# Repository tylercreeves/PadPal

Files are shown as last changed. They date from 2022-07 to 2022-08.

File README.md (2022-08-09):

# PadPal

> Author: Tyler Reeves, AKA T-Rex ([@tylercreeves](https://github.com/tylercreeves))

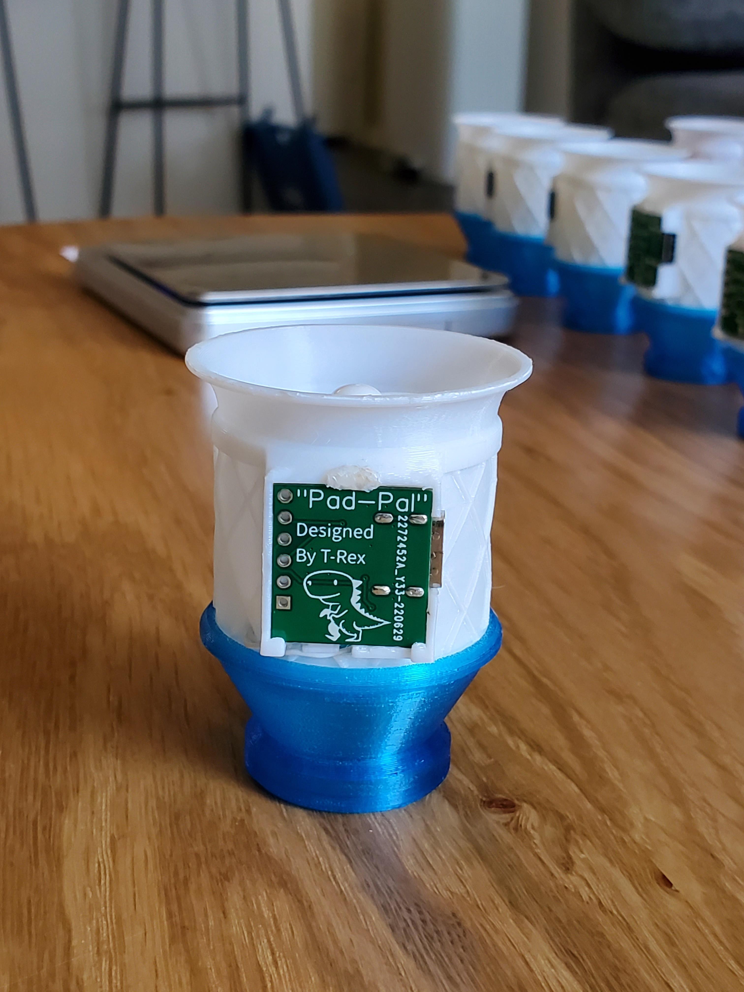
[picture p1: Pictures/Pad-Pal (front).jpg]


**An untralight electric sleeping pad inflator solution**

The PadPal is a bare bones, simple electric sleeping pad inflation device. The goal of this project is to make a sleeping pad inflator that us UL folks would not shun away in flavor of sore jaw muscles, empty lungs, and light heads.

Below is a breakdown of the project as well as how you can make your own. 

If making your own seems like a hassel, you can also purchase them from me for $44.00 shipped to the lower 48 states (contact me for shipping rates elsewhere) by reaching out to me via reddit u/tylercreeves

## Design

The PadPal is designed to leverage consumer grade 3D printing technology and consumer accessible PCB manufactures like JLCPCB. It is composed of 5 parts.

>**Part:** 3D printed fan duct housing

**Qty:** 1

>**Part:** 3D printed sleeping pad valve adapter

**Qty:** 1

>**Part:** 6x15mm coreless DC motor with .8mm shaft and micro JST connector

**Qty:** 1

>**Part:** 31mm 4 blade propeller with .8mm press fit shaft hole.

**Qty:** 1

>**Part:** PadPal V3 PCB with SMD

**Qty:** 1

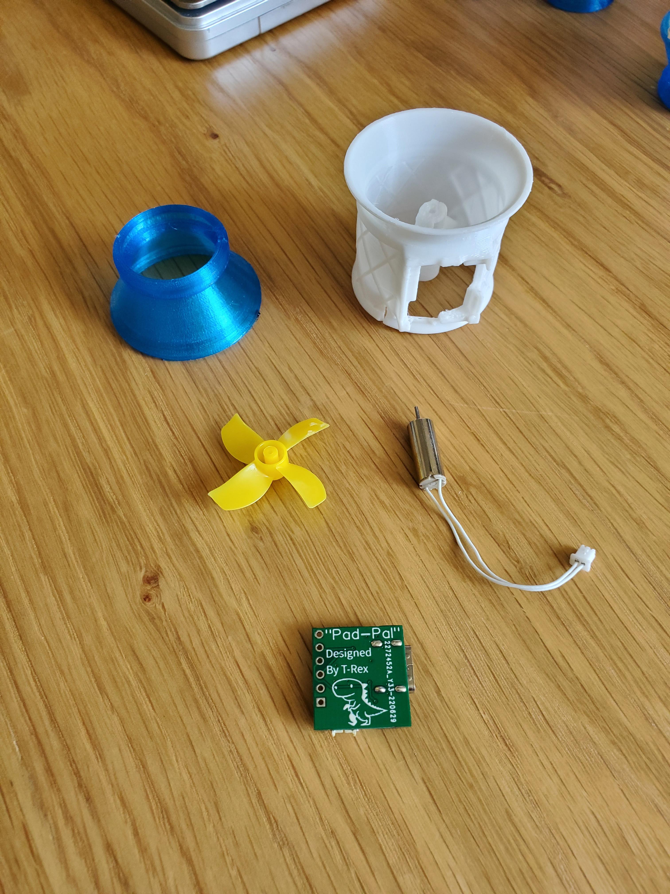
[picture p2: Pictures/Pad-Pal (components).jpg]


## 3D Printed Hardware

There are 2 user printed parts that compose the PadPals general body. Bellow are printing suggestions for each part.

>**Part:** PadPal_Duct_V3

**Material:** Polycarbonate

**Settings:** Use custom support structures to support the motor housing, bridges for the PCB housing, and chamerfered bridges from motor housing to inner fan duct. Here is a picture of the areas I added custom support enforcers. A brim may help prevent the Polycarbonate from warping.

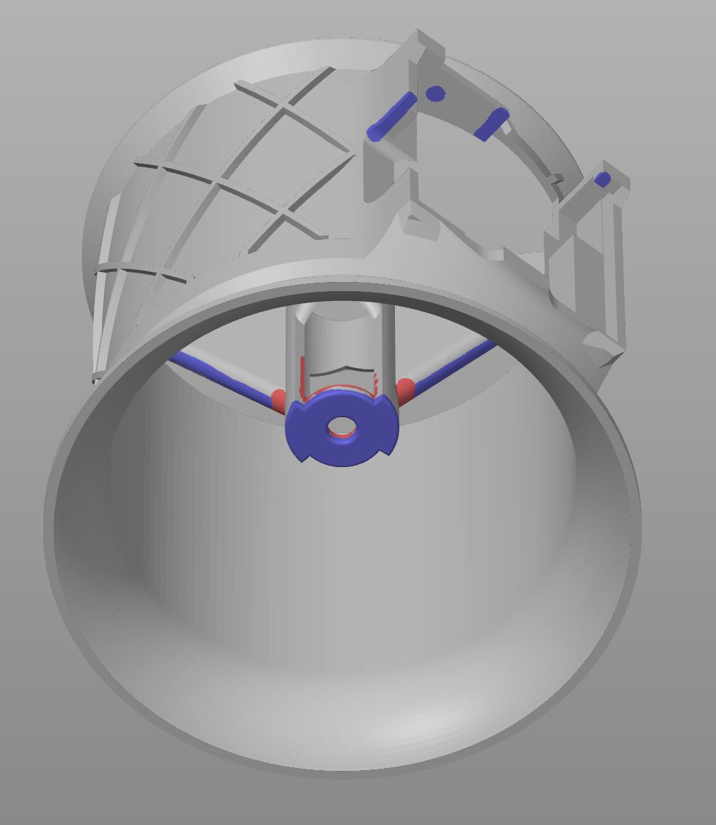
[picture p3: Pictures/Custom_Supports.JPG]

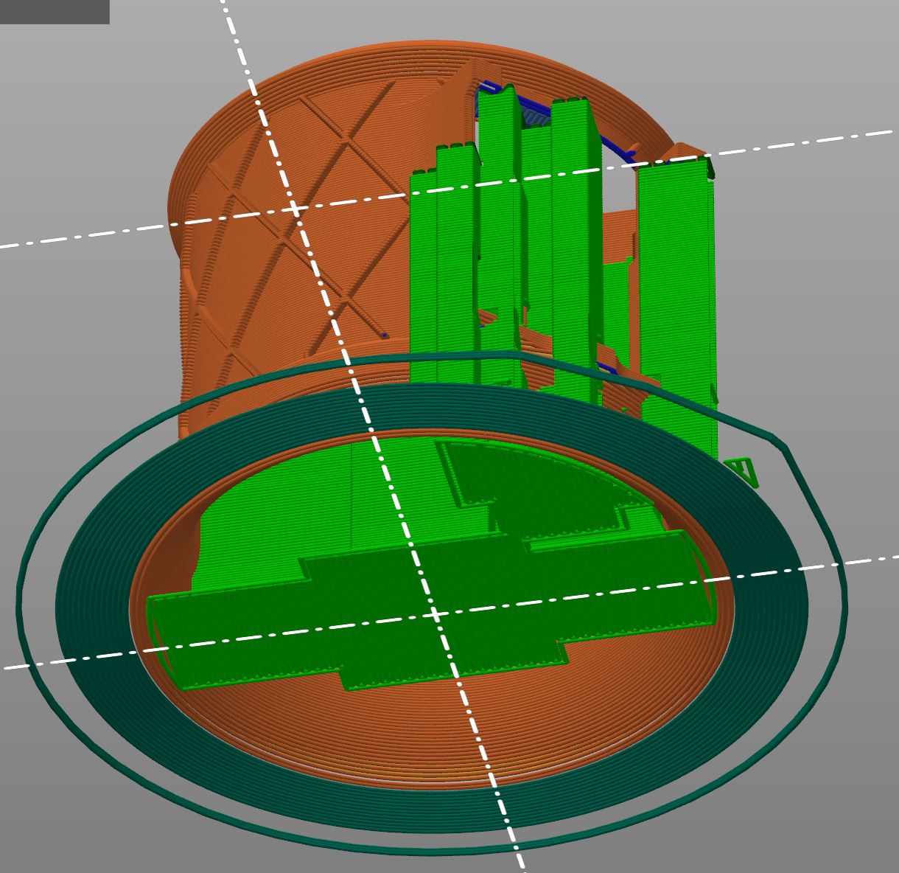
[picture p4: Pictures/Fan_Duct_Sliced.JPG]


>**Part:** PadPal_ThermarestWingLock_V3

**Material:** TPU

**Settings:** print with skinny end facing up, add a 2mm brim, no supports

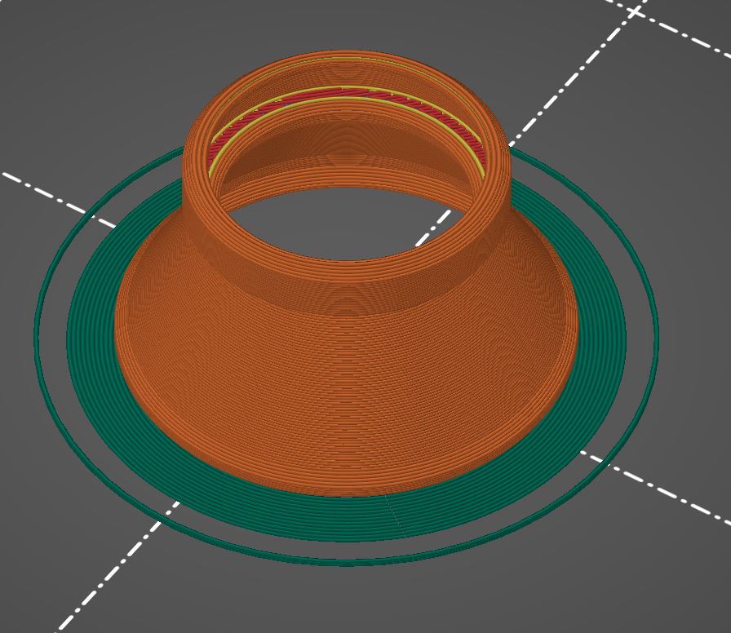
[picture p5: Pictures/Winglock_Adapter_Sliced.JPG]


## Code (Finite State Machine)

The PadPal utalizes an Attiny13ASU microcontroller that can be programmed to controlle the DC motor. I have programmed the MC with a finite state machine that works as follows. When you plug in the device, it waits 2 seconds before starting. After 2 seconds pass, it ramps up the fan to a specified speed. Once at specified speed it maintains that speed for a specified time. Once the specified time has ellapse, it will turn off the fan and enter sleep mode to avoid accidentally draining a forgetful hikers bacttery bank. To restart the PadPal, the user must unplug it and plug it in again.

## Making/Buying the Custom PCB

To get a custom motor controller PCB for this project, you have two options. One is to download the EDA GERBER files, BOM file, and source a manufactureur for the PCB as well as all the components. This board used SMD components and requires some decent skills in SMD soldering to pull off. It you go this route, there usually are minimum order quantities required for the PCB and components, so you may end up with a few extra boards.

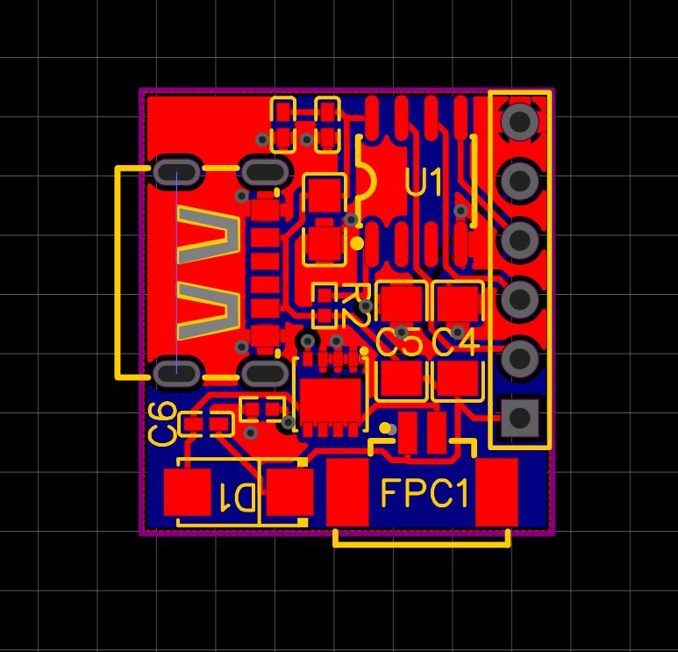
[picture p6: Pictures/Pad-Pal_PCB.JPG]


To save some of you the time and complexity of making and programming the boards yourself, you can contact me via reddit at u/tylercreeves where I sell the assembled and programmed boards for $12.18 shipped to the lower 48 states (contact me for special shipping rates elsewhere).

## Programming the PCB

Assuming you have gone the route of making your own boards, here is how to program the PadPal PCB. You will need to make an "Arduino as ISP". For this I used an Arduino Uno board and purchased a perferate "hat" board to solder up programmer with pogopins. Here are picture of the Arduino uno, custom "hat", and the two together.

 


First you will need to download the Arduino IDE if you havent done so. Next you need to flash the "Arduino as ISP" example sketch into the Arduino You will use to program your PadPal. Now you need to download the MicroCore liberary into your Arduino IDE so you can program the PadPal. Please watch [this video](https://www.youtube.com/watch?v=G2nVVtmKgWI&list=LL&index=113) of an unrelated project on how to do so by Electronics BD.

## Arduino as ISP Programmer Pin-Out

Here is a picture of my setup and Pin-Out of the headers on my custom motor control boards. You might have to do some clever mix and matching between my picture and the linked video untill I put up a complete pin-out for the arduino-ISP programmer I made.

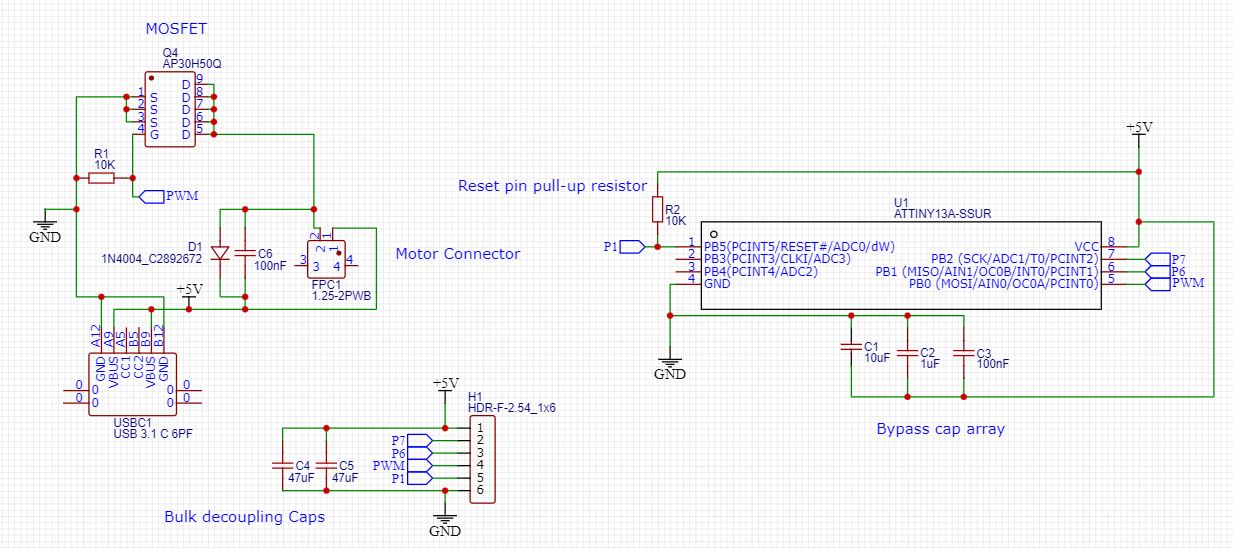
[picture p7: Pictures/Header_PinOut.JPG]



**Bellow is an FSM Diagram to assist in understanding the code so one can modify it.**

Review the FSM diagram along side the included code to get a sense of what is going on in the code. 

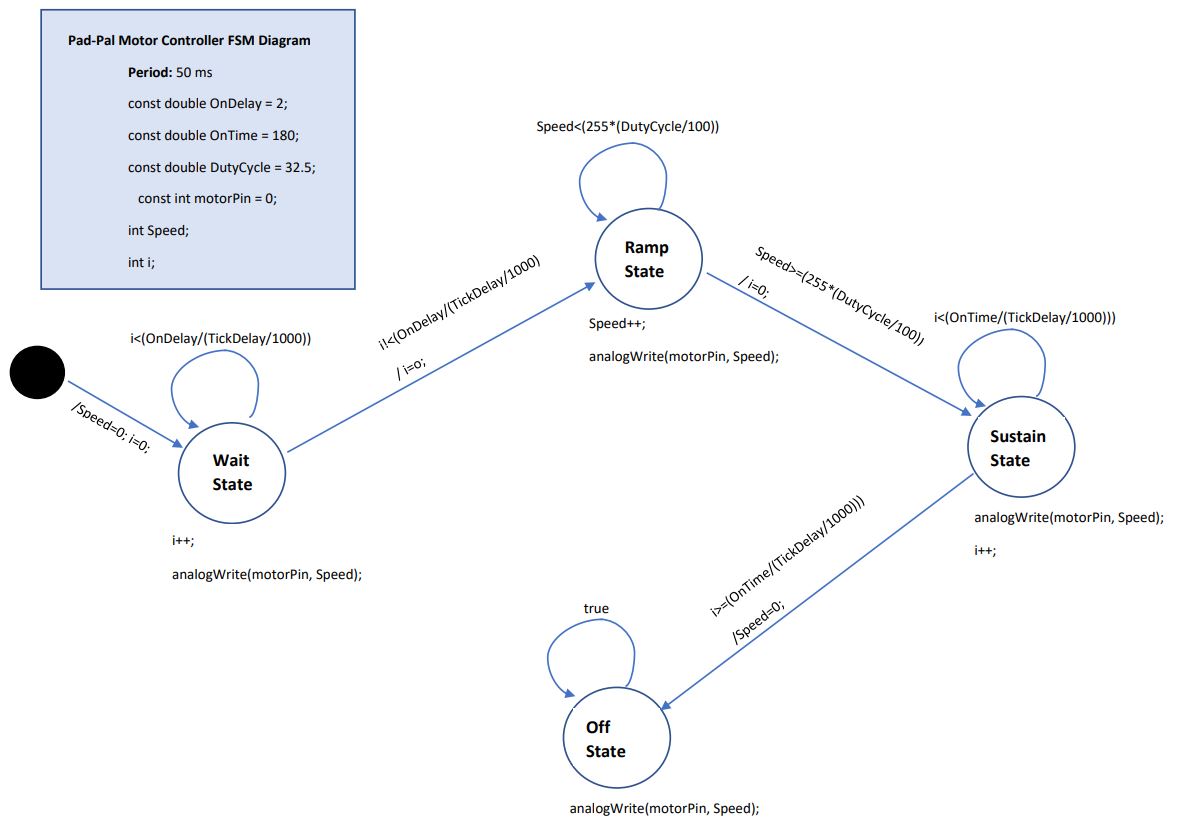
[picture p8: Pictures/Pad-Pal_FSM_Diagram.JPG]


## Assembly/Finishing

After you purchase a board, or finish making, soldering, and programming your own, you are ready for assembly! I'm not even going to tell you how, its pretty simple once all the parts are infront of you your ready. I'd suggest do the motor first, followed by the fan blade, then plugin the motor to the PCB and insert the PCB to its housing. Its a tight fit so you may need to get glever with some soft contact tools to push it in all the way.

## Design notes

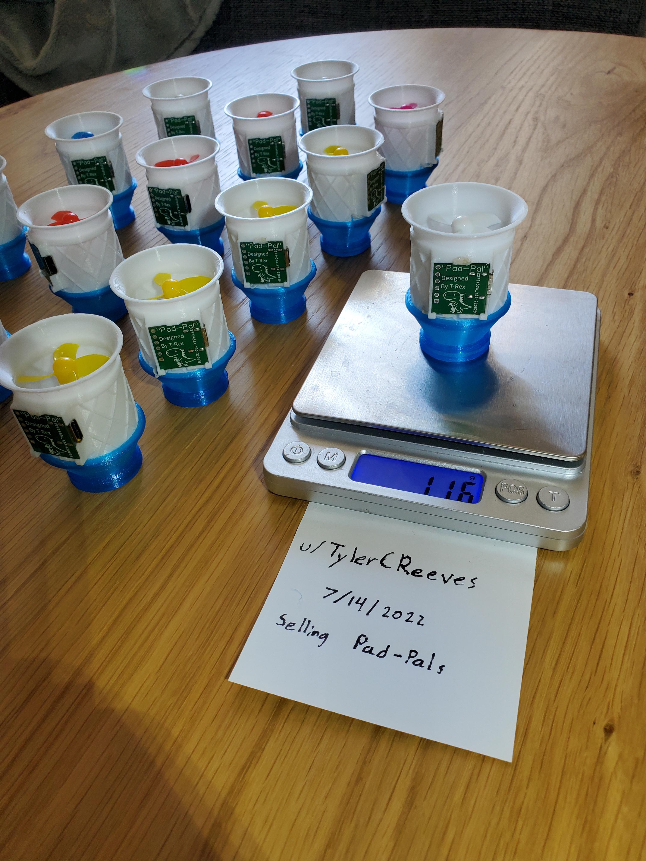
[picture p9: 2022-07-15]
Pictures/Pad-Pals (on scale).jpg

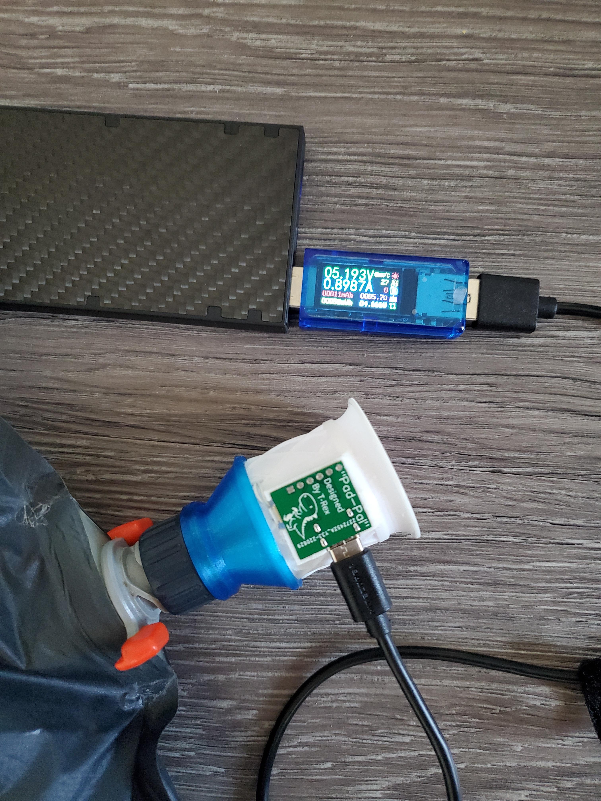
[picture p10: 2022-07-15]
Pictures/Pad-Pals (working).jpg

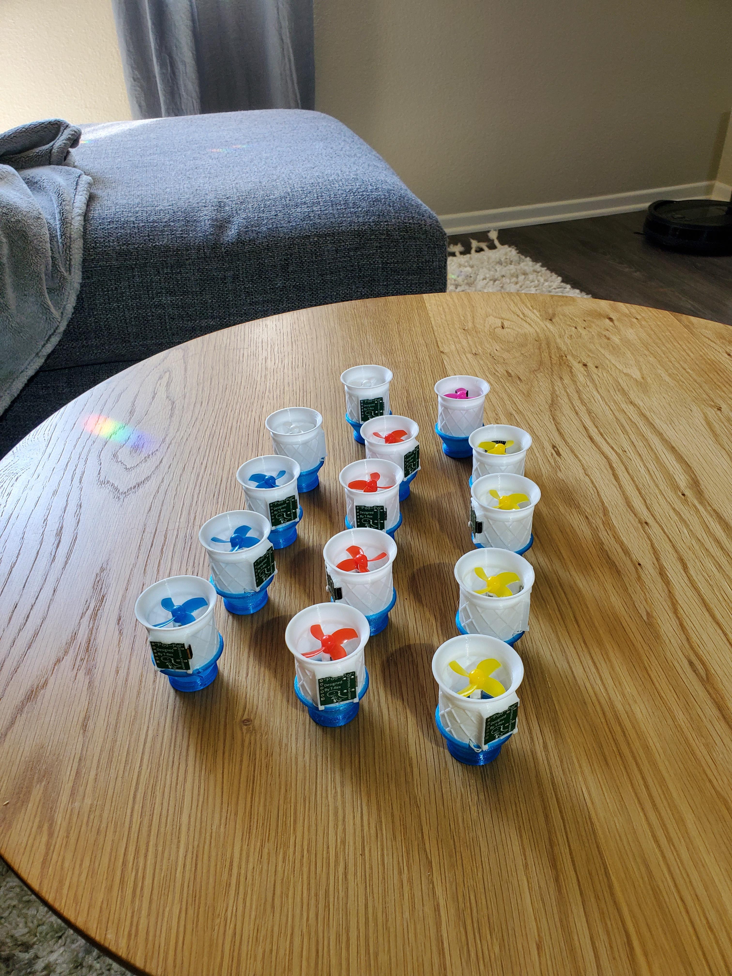
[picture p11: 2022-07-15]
Pictures/All the Pals.jpg

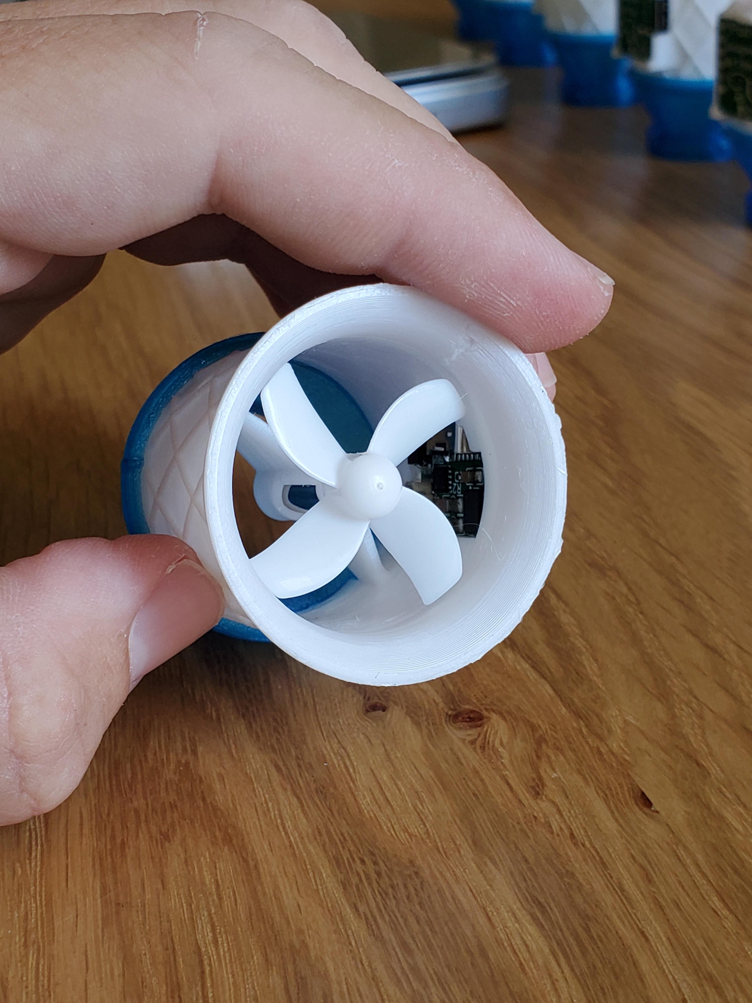
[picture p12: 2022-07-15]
Pictures/Pad-Pals (top).jpg

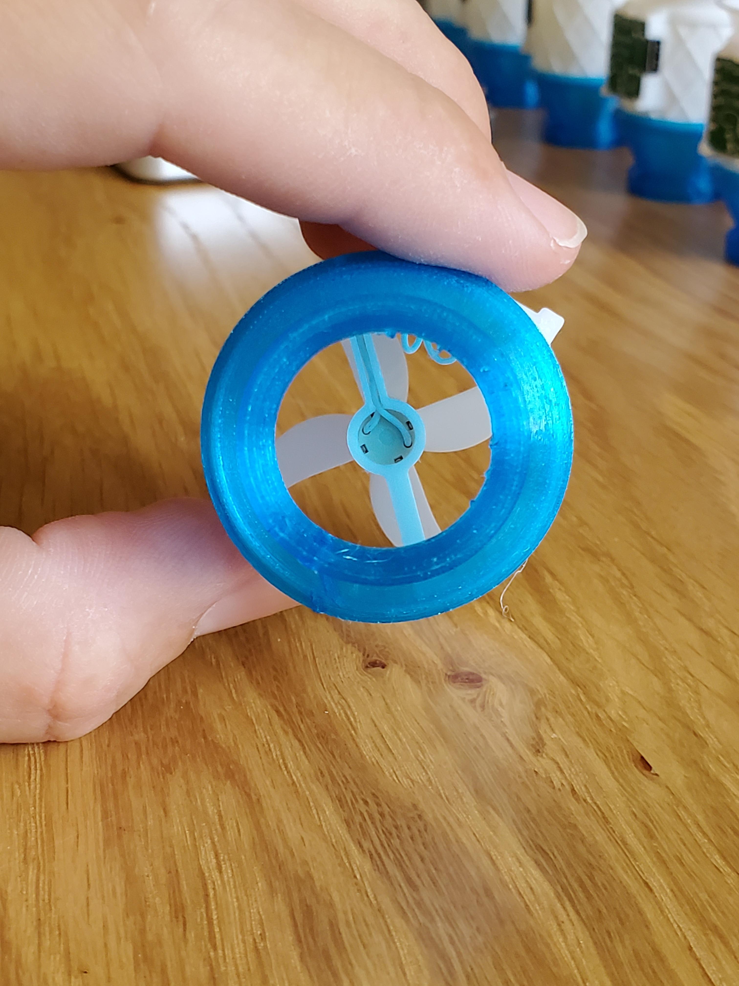
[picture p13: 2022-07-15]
Pictures/Pad-Pal (bottom).jpg

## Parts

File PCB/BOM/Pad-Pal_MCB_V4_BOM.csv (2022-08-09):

ID | Name | Designator | Footprint | Quantity | Manufacturer Part | Manufacturer | Supplier | Supplier Part
1 | 10uF | C1 | C0805 | 1 | GCM21BR71A106KE22L | MuRata | LCSC | C126586
2 | 1uF | C2 | C0402 | 1 | GCM155C71A105KE38D | Murata Electronics | LCSC | C126521
3 | 100nF | C3,C6 | C0402 | 2 | CC0402JRX7R8BB104 | YAGEO | LCSC | C541465
4 | 47uF | C4,C5 | C1206 | 2 | CL31A476MPHNNNE | SAMSUNG | LCSC | C96123
5 | 1N4004_C2892672 | D1 | SMA_L4.3-W2.6-LS5.1-RD | 1 | 1N4004 | YONGYUTAI(永裕泰) | LCSC | C2892672
6 | 1.25-2PWB | FPC1 | CONN-SMD_2P-P1.25_DEALON_1.25-2PWB | 1 | 1.25-2PWB | DEALON(德艺隆) | LCSC | C2905009
7 | HDR-F-2.54_1x6 | H1 | HDR-F-2.54_1X6 | 1 |  |  | LCSC | C40877
8 | AP30H50Q | Q4 | DFN-8_L3.2-W3.1-P0.65-LS3.4-BL | 1 | AP30H50Q | ALLPOWER(铨力) | LCSC | C2849568
9 | 10K | R1,R2 | R0402 | 2 | RT0402BRD0710KL | YAGEO | LCSC | C190095
10 | ATTINY13A-SSUR | U1 | SOIC-8_L5.0-W4.0-P1.27-LS6.0-BL | 1 | ATTINY13A-SSUR | MICROCHIP | LCSC | C40382
11 | 5.1kΩ | U2,U3 | R0402 | 2 | HPCR0402F5K10K9 | ResistorToday | LCSC | C365032
12 | USB 3.1 C 6PF | USBC1 | USB-C-SMD_TYPE-C-USB-13 | 1 | - | LCSC | LCSC | C168701

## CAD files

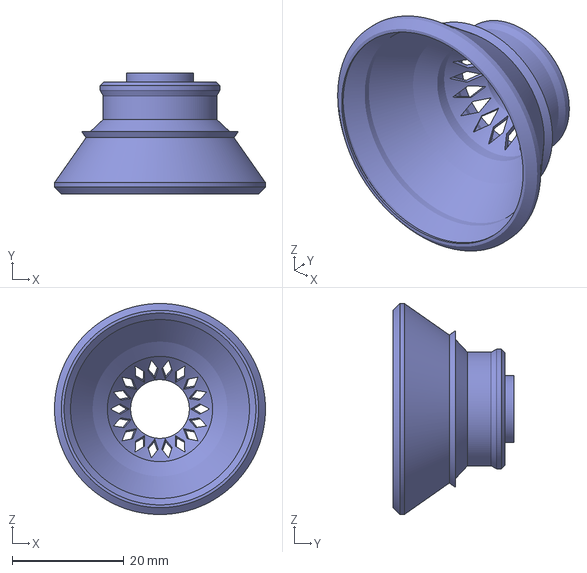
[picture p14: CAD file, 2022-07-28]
Hardware_Files/Mesh_Files(for pirnitng)/Exped Sinmat Addapter/PapPal_ExpedSinmat_1.2.3mf
37.8 x 21.6 x 37.8 mm

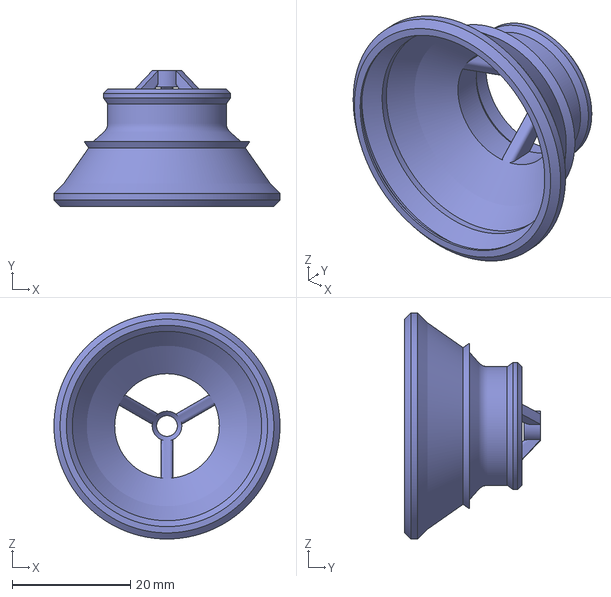
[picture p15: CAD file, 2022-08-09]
Hardware_Files/Mesh_Files(for pirnitng)/Sea to Summit Addapters/Seas2Summit_V1.3.3mf
38.2 x 22.9 x 38.2 mm

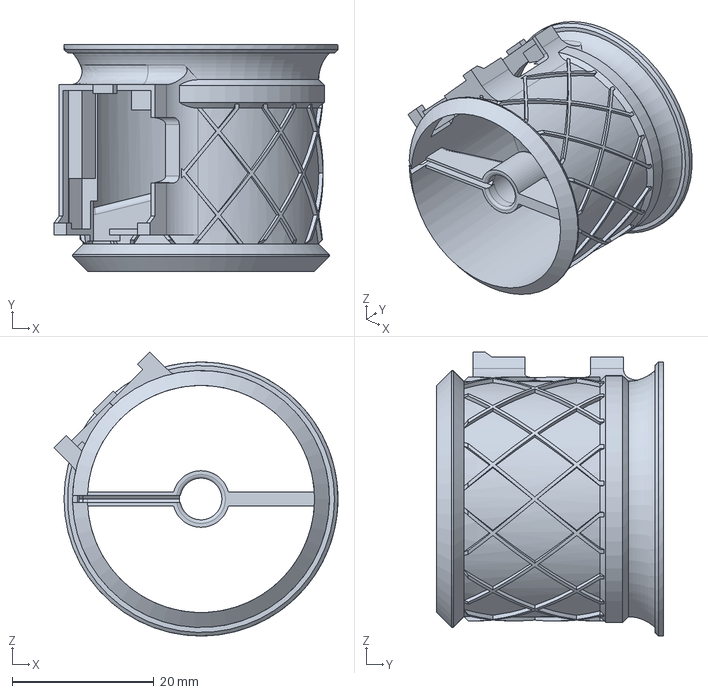
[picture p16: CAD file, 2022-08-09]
Hardware_Files/CAD_Files/Fan Duct/Duct Housing_V3.2.step
40.0 x 31.9 x 40.0 mm

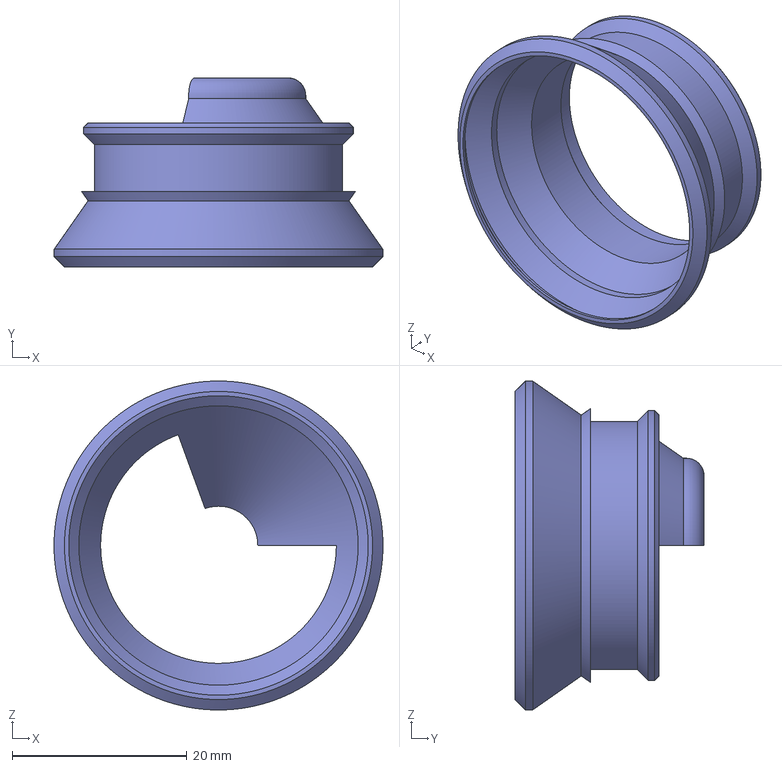
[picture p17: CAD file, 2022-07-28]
Hardware_Files/Mesh_Files(for pirnitng)/Big Agnes Pad Addapters/Big Agnes Valve Adapter 1.1.3mf
37.7 x 21.7 x 37.7 mm

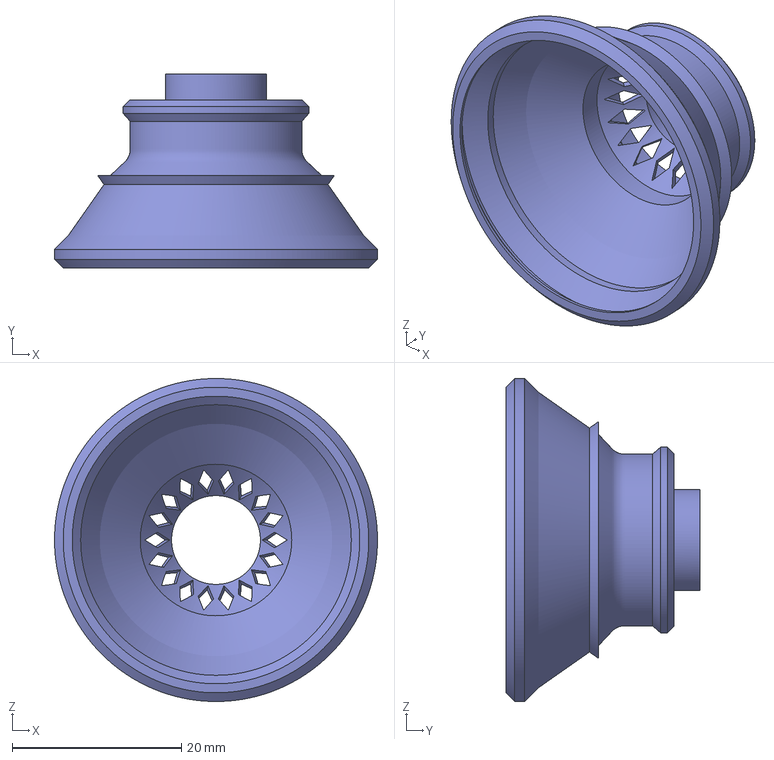
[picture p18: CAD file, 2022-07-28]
Hardware_Files/Mesh_Files(for pirnitng)/Exped Sinmat Addapter/PapPal_ExpedSinmat_V2.3mf
38.2 x 22.9 x 38.2 mm

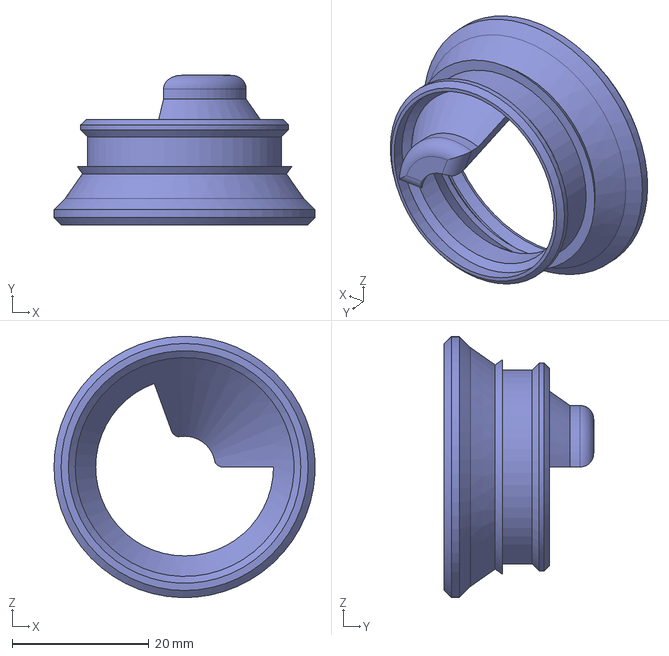
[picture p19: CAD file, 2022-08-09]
Hardware_Files/CAD_Files/Valve Adapters/Big Agnes Valve Addapter.step
38.2 x 21.9 x 38.2 mm

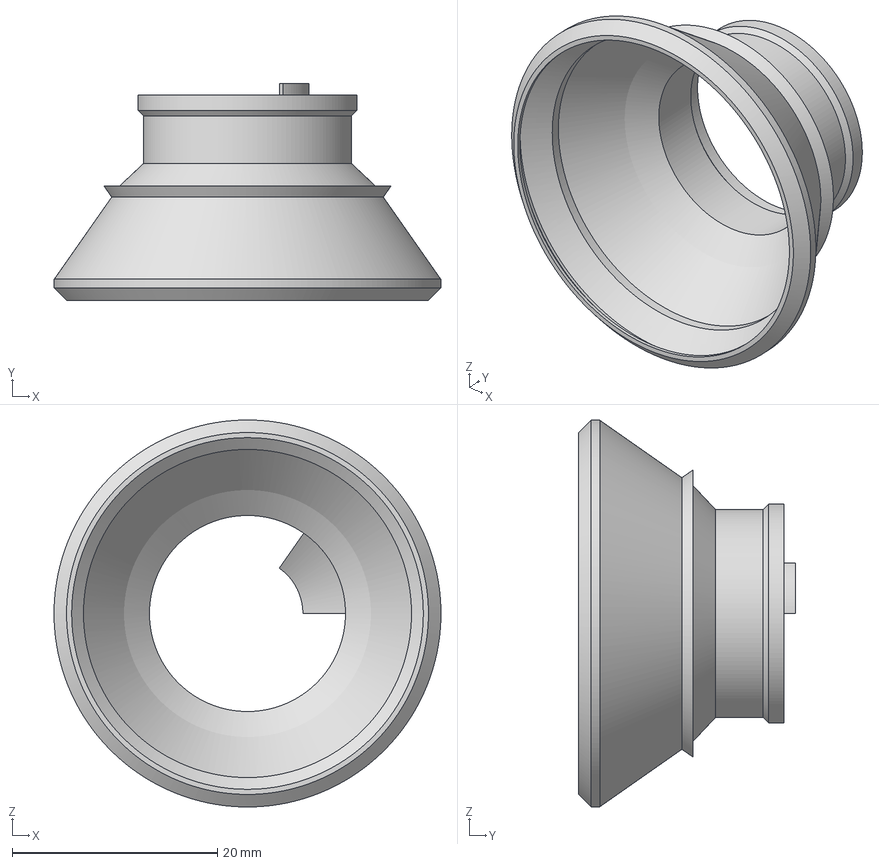
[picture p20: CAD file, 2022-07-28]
Hardware_Files/Mesh_Files(for pirnitng)/Exped Sinmat Addapter/PapPal_ExpedSinmat_1.1.3mf
37.8 x 21.1 x 37.8 mm

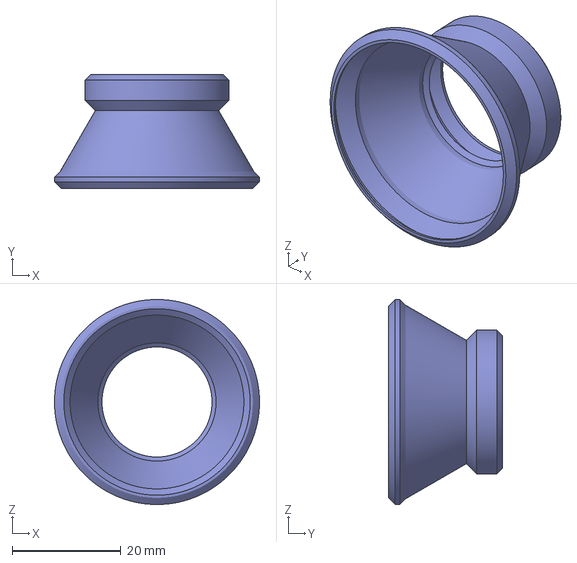
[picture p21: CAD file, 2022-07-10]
Hardware_Files/Mesh_Files(for pirnitng)/Thermarest Adapters/PadPal_ThermarestWingLock_1.3.3mf
37.7 x 21.0 x 37.7 mm

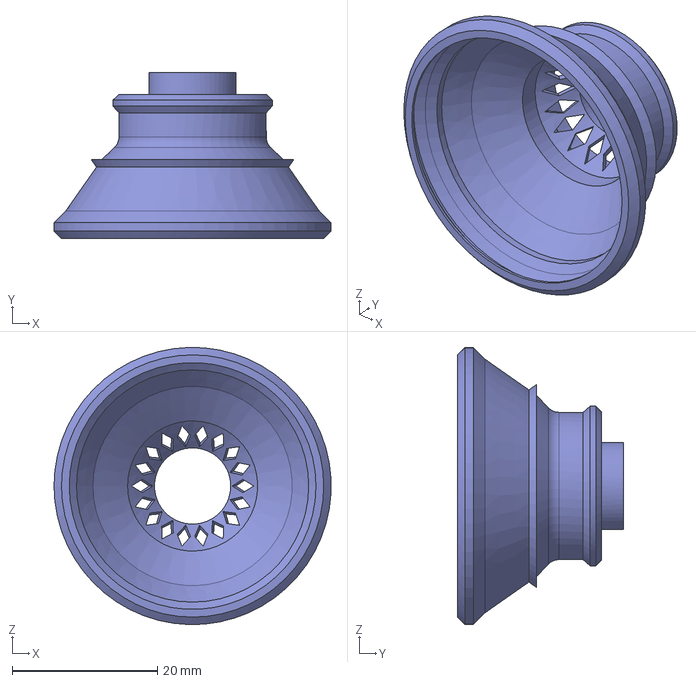
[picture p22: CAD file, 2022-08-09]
Hardware_Files/CAD_Files/Valve Adapters/Exped Sinmat UL Valve Adapter.step
38.2 x 22.9 x 38.2 mm

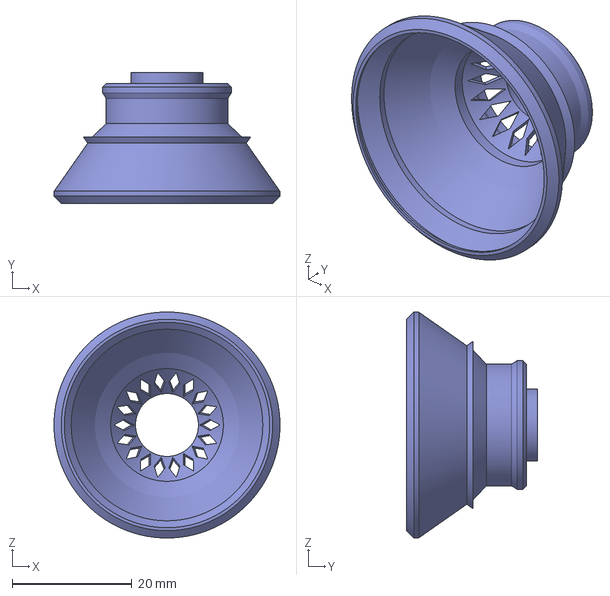
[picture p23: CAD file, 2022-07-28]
Hardware_Files/Mesh_Files(for pirnitng)/Exped Sinmat Addapter/PapPal_ExpedSinmat_1.3.3mf
37.8 x 21.9 x 37.8 mm

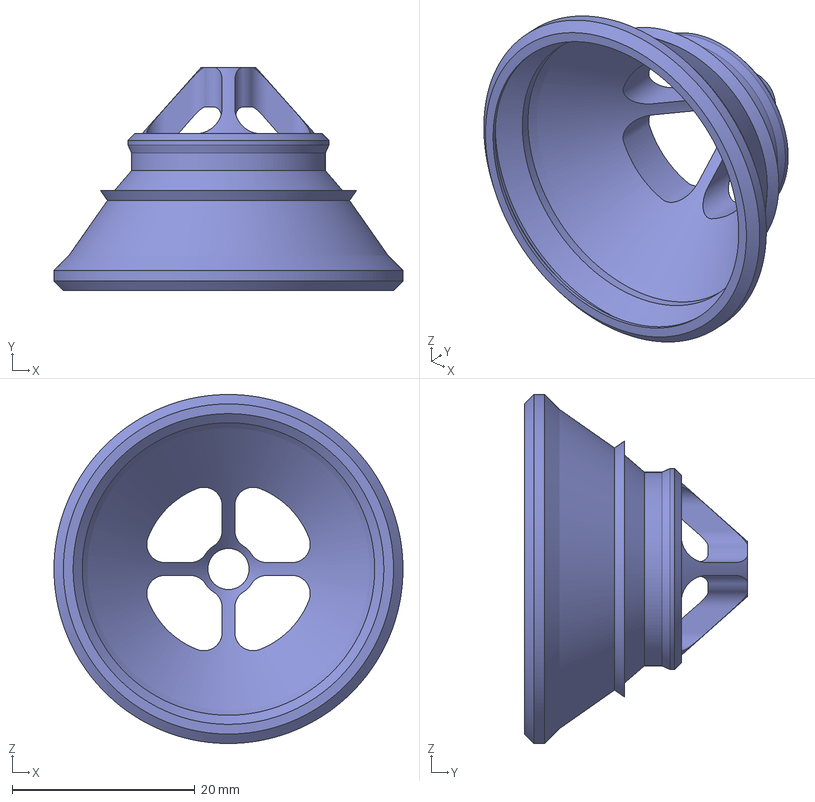
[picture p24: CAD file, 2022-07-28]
Hardware_Files/Mesh_Files(for pirnitng)/Nemo Pad Coupler/Nemo_CoupLer_V1.3.3mf
38.2 x 24.4 x 38.2 mm

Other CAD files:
Hardware_Files/CAD_Files/Valve Adapters/Sea to Summit Valve Addapter.step
Hardware_Files/Mesh_Files(for pirnitng)/Fan_Duct/PadPal_Duct_V3.3.3mf
Hardware_Files/CAD_Files/Valve Adapters/Nemo Tensor Insulated Valve Addapter.step
Hardware_Files/Mesh_Files(for pirnitng)/Exped Sinmat Addapter/PapPal_ExpedSinmat_1.9.3mf
Hardware_Files/Mesh_Files(for pirnitng)/Big Agnes Pad Addapters/Big_Agnes_Valve_Adapter_V1.5.3mf
Hardware_Files/Mesh_Files(for pirnitng)/Exped Sinmat Addapter/PapPal_ExpedSinmat_1.6.3mf
Hardware_Files/CAD_Files/Valve Adapters/PadPal_ThermarestWindLockValve_V3.step
Hardware_Files/CAD_Files/Fan Duct/Duct Housing_V3.1.step
Hardware_Files/CAD_Files/Valve Adapters/Old Nemo Twist Valve Addapter.step
Hardware_Files/CAD_Files/Valve Adapters/Old Thermarest Twist Valve Adapter.step
Hardware_Files/Mesh_Files(for pirnitng)/Big Agnes Pad Addapters/Big_Agnes_Valve_Adapter_V1.2.3mf
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

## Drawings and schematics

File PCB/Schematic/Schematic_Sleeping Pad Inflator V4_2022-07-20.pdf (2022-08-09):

## MOSFET

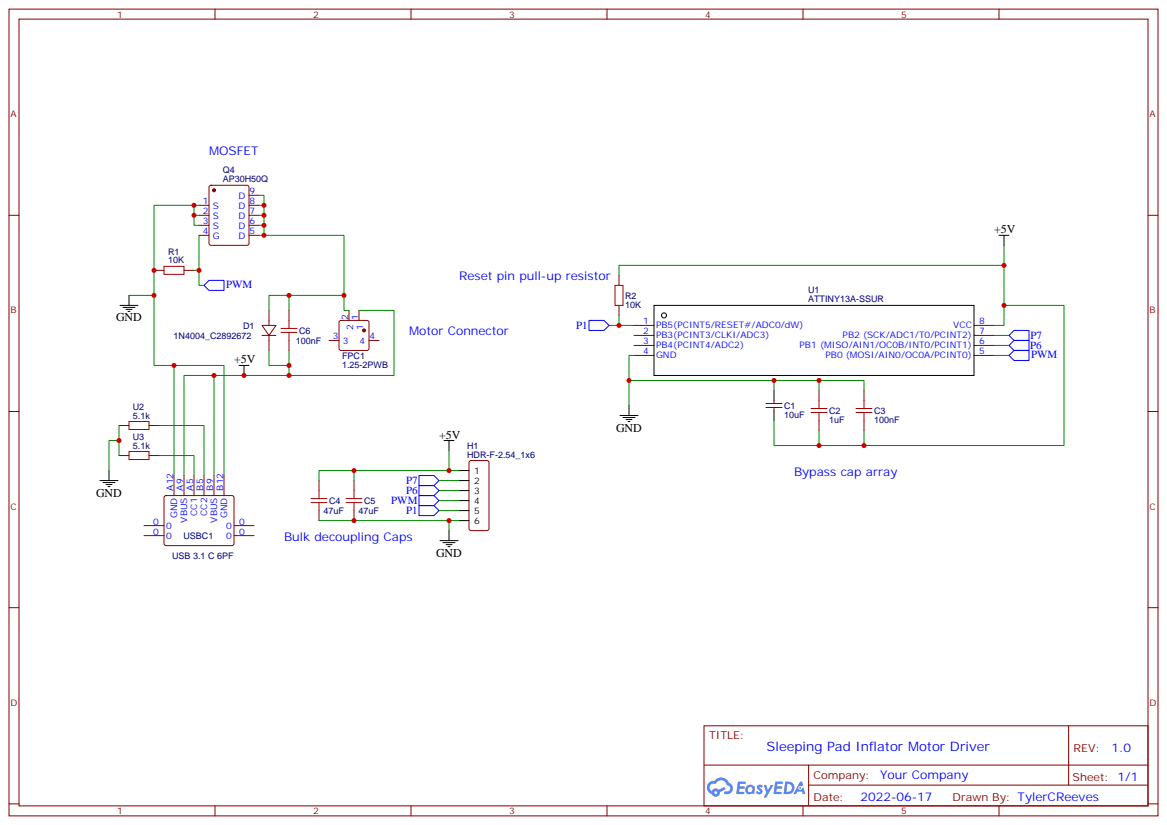
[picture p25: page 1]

Reset pin pull-up resistor

GND B12 VBUS B9 CC2 B5 CC1 A5 VBUS A9 GND A12

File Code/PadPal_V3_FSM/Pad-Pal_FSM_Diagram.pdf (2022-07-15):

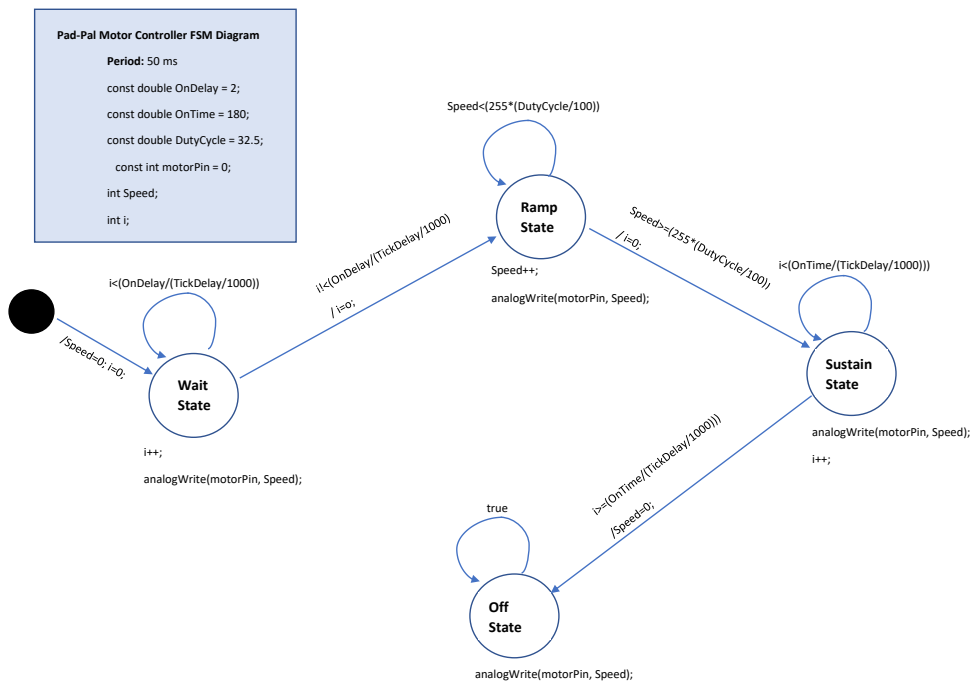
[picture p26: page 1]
i<(OnDelay/(TickDelay/1000)); Speed<(255*(DutyCycle/100)); Speed++;; i<(OnTime/(TickDelay/1000))); true; Period: 50 ms; int Speed;; int i;; Wait State; Ramp State; Sustain State; Off State

Pad-Pal Motor Controller FSM Diagram

const double OnDelay = 2;

const double OnTime = 180;

const double DutyCycle = 32.5;

const int motorPin = 0;

analogWrite(motorPin, Speed);

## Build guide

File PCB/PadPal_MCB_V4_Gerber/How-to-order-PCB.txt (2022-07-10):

How to Order PCB

Please refer to:
https://docs.easyeda.com/en/PCB/Order-PCB

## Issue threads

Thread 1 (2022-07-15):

USBC PD issue

qxtman, 2022-07-15:
Hey, I don't have mine in hand yet, but going off of Schematic V3,
At present, you do not have any resistors on the CC1 or CC2 lanes of the USB C connector.
I believe that those resistors are required when using a propper USB C supply.
Attaching a 5.1k pull down resistor to each pin will (should) re enable USBC to USBC functionality.
I have mine on the way, I will see if I can update my model to prove it out.

There are more details with USB C PD, about forcing lower maximum current, but I do not have enough details on that at present.

tylercreeves, 2022-07-20:
Thanks qxtman!!
Just created a new branch for motor control board V4 where I'm trying to implement the USB-C to USB-C functionality.
I took a V3 board and did a hack job at adding the resistors as described. Interestingly, it worked via USB-C ports on both my power banks, but did not work from a USB-C wall powered power source. IDK whats going on there but it really only has to work with power banks so that left me satisfied enough to implement the changes in a new board.
I'll be uploading the V4 board Gerber files later today, and I should have 20 V4 boards coming in the mail soon (about a week). I'll merge the branch back with main if everything pans out after testing.

tylercreeves, 2022-07-28:
V4 Boards are in and undergoing testing. They appear to work flawlessly : ) I plan to be merging the Motor_Control_Board_V4 branch with main soon.

tylercreeves, 2022-08-10:
I think its solved, V4 board have been working great and snuck them into a few customer Pad-Pals with no issues. I'll be closing this issue for now unless something else pops up.

Closed 2022-08-10.

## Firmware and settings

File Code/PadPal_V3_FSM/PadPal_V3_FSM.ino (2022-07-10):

/*Author: Tyler Reeves
 *Purpose: A finite state machine to control the motor of a sleeping pad inflator.
 *This program works by transitioning between states (each state performs a unique function) based on user selected transition conditions.
 *
*/


//Inflator user paramiters
const double OnDelay = 2;         //OnDelay is the time in seconds the inflator will wait to start the fan after being pluged in
//const double RampDelay = 5;     //time in seconds the fan will ramp up to max speed. Note, not compatible with AttinyA13 MC, uncomment for additional functuionality if you'r using an MC with more flash memmory
const double OnTime = 120;        //OnTime is the time the inflator will stay on in seconds.
const double DutyCycle = 20;      //Max fan speed in terms of percentage. EX: if DutyCycle = 35, then fan will max out at 35% speed. WARNING, depending on motor installed, DutyCycle >= 45 may cause overheating and damage

//peramiters governing finite state machine behavior
const int motorPin = 0;           //Which microcontroller pin sends out the PWM signal?
const double TickDelay = 50;      //Time between state transitions in milliseconds

//Finite State Machine variables
int Speed;                        //Speed is used to ramp up and down fan speed during state ticks. If Speed == 0 no fan, if Speed==255 Max fan.
int i;                            //used to keep track of # of ticks through a given state of the finite state machine

enum States{Wait, Ramp, Sustain, Off} State = Wait; //Declare the states of the finite state machine and set the initial starting state.


void setup()
{
  pinMode (motorPin, OUTPUT);
  Speed=0;
  i=0;
  
}

void Tick(){
  switch(State){ // State transitions
    case Wait:
    if(i<(OnDelay/(TickDelay/1000))){ //Check i to see if power has been on for less than onDelay time
        State = Wait;
      }
      else {
        i=0;
        State = Ramp;
      }
    break;
      
    case Ramp:
      if(Speed<(255*(DutyCycle/100))){ //replace 20 with (255*(DutyCycle/100))
        State = Ramp;
      }
      else if(Speed>=(255*(DutyCycle/100))){
        i=0;
        State = Sustain;
      }
    break;
    
    case Sustain:
      if(i<(OnTime/(TickDelay/1000))){ //Check i to see if fan has ran for its max time. Sustain power if not.
        State = Sustain;
      }
      else if(i>=(OnTime/(TickDelay/1000))){ //Check i to see if fan has run for its max time. Power off by changing speed to 0 if true.
        Speed = 0;
        State = Off;
      }
    break;

    case Off:
      State = Off;
    break;
  }

  switch(State){ // State Actions
    case Wait:
      i++;
      analogWrite(motorPin, Speed);
    break;
      
    case Ramp:
      //This block of code does not work with attinyA13 MC. If you change the MC, uncommenting this code and its accompening const variable in setup
      //will allow one to define the interval of time in which the ramp up to max speed happens
      //===============================================
      /*i++;
      if((i*(TickDelay/1000))==(RampDelay/DutyCycle)){
      Speed++;
      analogWrite(motorPin, Speed);
      i=0;
      }*/
      //==============================================
      Speed++;
      analogWrite(motorPin, Speed);
    break;
    
    case Sustain:
      analogWrite(motorPin, Speed);
      i++;
    break;

    case Off:
    analogWrite(motorPin, Speed);
    break;
  }
}




void loop()
{
  Tick();
  delay(TickDelay);
}

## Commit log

2022-07-10 Add files via upload
    Added source files for code, hardware, CAD, and schematics
    Still need BOM, and PCB files.
    [PadPal_Duct_V3.3mf, PadPal_Duct_V3.step, PadPal_ThermarestWindLockValve_V3.step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]
2022-07-10 Add files via upload
    Added PCB gerber files and BOM files
    [Drill_PTH_Through.DRL, Gerber_BoardOutlineLayer.GKO, Gerber_BottomLayer.GBL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]
2022-07-20 Motor Control Board V4
    Added gerber files and documentation for MCB V4
    [Drill_PTH_Through.DRL, Gerber_BoardOutlineLayer.GKO, Gerber_BottomLayer.GBL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]
2022-07-28 Added new Valve adapters for many more pads
    Added files for valve adapters to make the PadPal compatible with Nemo pads, Big Agnes Pads (with double flat valve), Exped pads (also works on REI flash pads), and older Thermarest pads with their c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
    [Big Agnes Valve Adapter 1.1.3mf, Big_Agnes_Valve_Adapter_V1.2.3mf, Big_Agnes_Valve_Adapter_V1.3.3mf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]
2022-08-09 Added More Pad Adapeters
    New files for Sea to Summit valve adapter and SHMAYBE an old Nemo twist valve (untested!)
    [OldNemo_Twist Valve_1.1.3mf, PadPal_Duct_V3.2.3mf, PadPal_Duct_V3.3.3mf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]
2022-08-09 Added STEP Files for new pad valve Adapters
    [Big Agnes Valve Addapter.step, Duct Housing_V3.1.step, Duct Housing_V3.2.step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]
